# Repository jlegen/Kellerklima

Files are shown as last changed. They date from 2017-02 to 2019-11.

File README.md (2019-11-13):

# Kellerklima
## Arduino-based humidity controller with indoor and outdoor sensors for fan control

I made this device to dry my (and others :) cellars by mostly making use of the times when the *absolute* humidity outdoors is lower than indoors. 
For this, two sensors are used to measure humidity and temperature, indoors and outdoors.
Though this seems to be quite a common design, i only found some rather costly commercial products. This one mostly uses cheap and popular modules.

## Basic principle
Temperature and humidity values from inside and outside are used to calculate the absolute humidity. If the outside is less humid than the inside, the fan is started (or, alternatively, the window is opened, if an opener is used instead of a fan).
There's a maximum fan runtime to be configured. After this time, either the fan is paused, or - using the 2nd relay - a dehumidifier unit can be started for a set period of time.
This repeats until the target humidity value for the inside is reached, or one of the user-defined criterias change:
* fan and dehumidifier only run if the inside humidity is above the trigger value
* fan only runs if inside temperature is above a minimum value
* fan only runs if outside temperature is above a minimum value
* fan and dehumidifier only run if the runtime limit per day (24h) is not reached yet

Defaults are: 
* dew point difference between indoors and outdoors >= 3: switch fan on
* dew point difference between indoors and outdoors < 1: switch fan off
* humidity hysteresis for trigger: 1 
	* indoor humiditity >= <trigger value>: switch fan/dehumidifier on
	* indoor humiditity < <trigger value - 1>: switch fan/dehumidifier off

## Implementation

The regulation makes use of configurable hysteresis values for activation and deactivation, to avoid "flapping", and a fan being turned on and off too quickly.
All parameters can be configured using the rotary encoder and a menu system with the 1602 LCD.
Optionally, if an ESP-01 module with ESP-Link (https://github.com/jeelabs/esp-link) is equipped, all parameters can be set using telnet. 
This ESP-01 module also allows to remotely flash the arduino code of the controller, and to monitor all activities of the control box remotely. Parameters can be defined using simple commands, and also fan or dehumidifier can be switched on and off, overriding the regulation.
the libraries used are commented in the code.

Update: It turned out that the DHT22 sensors are cr*p, they "wear out" quite quickly, showing wrong humidity data after a few weeks.
To be able to make use of better quality I2C sensors like BME280 or SHT31, i added an I2C booster/bus driver IC to allow for the long(er) wires i needed. For me, 10m do work just fine with SHT31, there are reports that up to 100m are possible, too.
Additionally, i did not manage to get the SLIP protocol running reliably using the ESP-Link, but i still regard the ESP-01 as useful, since the arduino not only can be flashed "OTA" using ESP-link, the new version also allows to monitor the arduino's activities using EPS-link's "µC Console", and the whole thing can be controlled remotely using a set of commands to set temperatures and other parameters. 
Next hardware revision should probably use an ESP module as controller... 

Update 2: Meanwhile, the system is running for more than a year in "production". Works like a charm... :-)

# Gallery

box in normal run mode; the LCD is switched off after a few minutes of inactivity

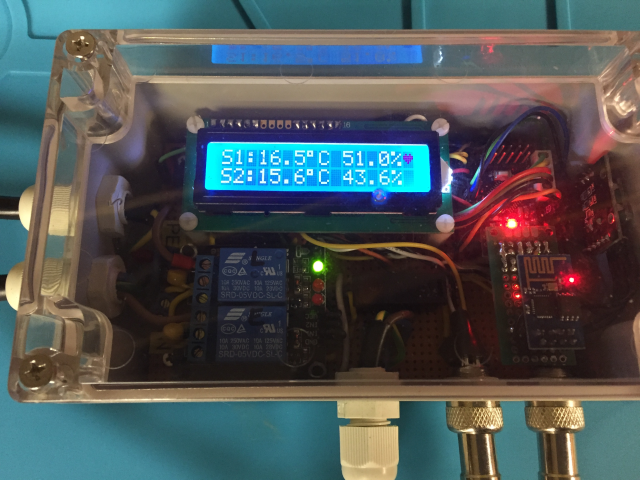
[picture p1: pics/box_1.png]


rotary encoder at the right - is used to scroll through values, testing the relay, and to set most parameters

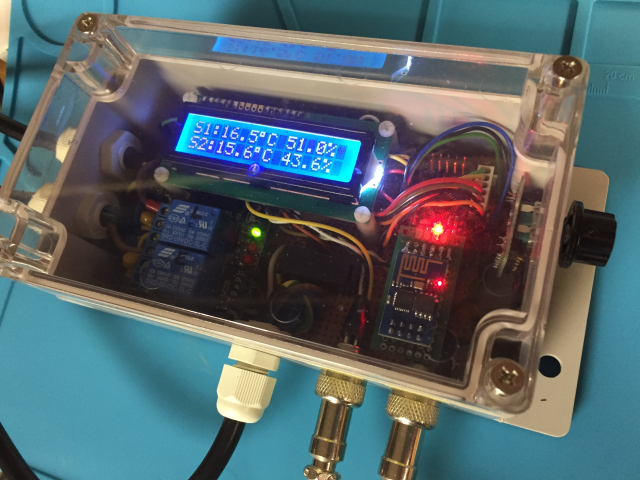
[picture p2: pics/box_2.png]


PCB version finally ready (V1.2)
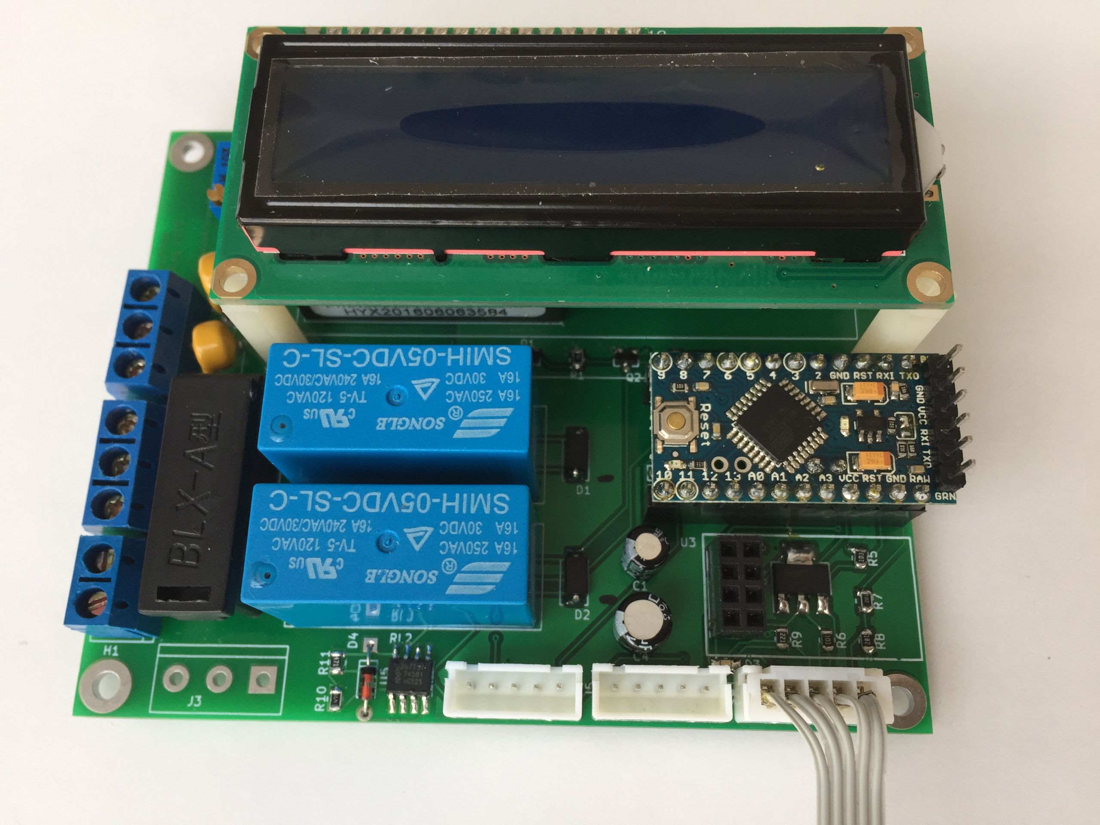
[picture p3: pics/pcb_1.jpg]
1st PCB version


new PCB for sensors - tailored to fit into cheap waterproof boxes (65X58X35mm)
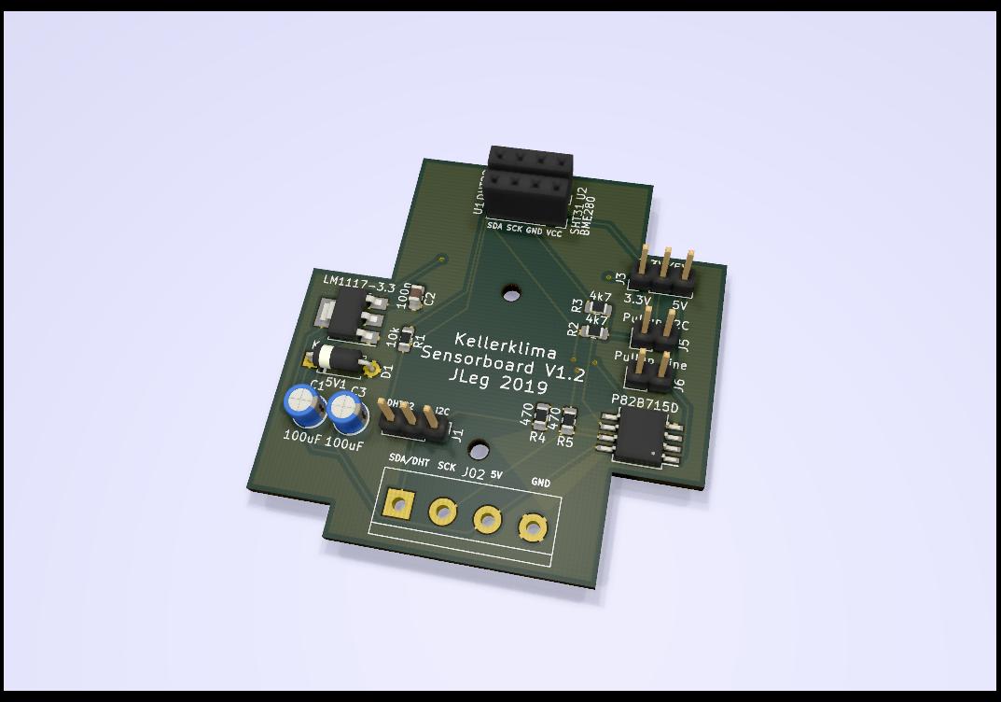
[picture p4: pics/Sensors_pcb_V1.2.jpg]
Sensor pcp 1.2


like these
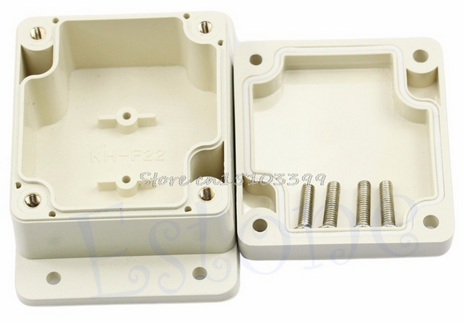
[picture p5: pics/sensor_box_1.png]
box_1

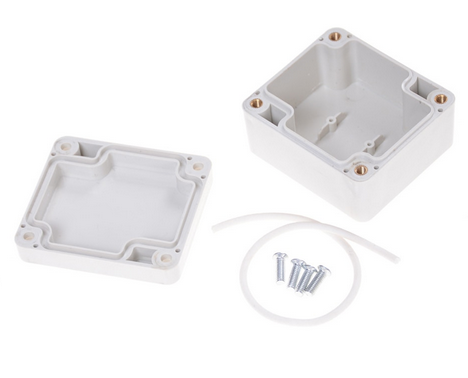
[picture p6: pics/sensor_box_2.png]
box_2


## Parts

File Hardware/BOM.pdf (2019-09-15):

Kellerklima 1.2
Humidity Controller

Main Controller
Arduino Pro Mini | 1 | check position of A4 and A5 (I2C)
Rotary encoder | 1 | generic type or module
Buzzer (passive), 12x9.5RM7.6 | 1
LCD 1602 | 1 | HD44780, parallel/4 bit mode
Case | 1
M12 cable gland (Verschraubung) | 3
SP16/GX16 4p cable connector | 2
PCB | 1 | JLCPCB
Relais 5V, Songle | 2 | SMIH-05V SL-A
Power HLK-PM01 | 1
JST connectors 1x04_P2.50mm | 3
5.1V Zehner | 1
P82B715D I2C Booster | 1
MOV (VDR), 420V | 2
ESP-01 | 1 | optional
Terminal 3p | 3
Terminal 2p | 1
Switch | 1
LM1117-3.3 | 1
BC846BS SOT3 | 2
Fuse holder | 1

Sensors (x 2)
SHT31 module | 2
SP16/GX16 4p cable connector | 2
cable, 4p, shielded (m) | 10
Case | 2
PCB | 2
5.1V Zehner | 2
LM1117-3.3 | 2
P82B715D I2C Booster | 2
Terminal 4p | 2

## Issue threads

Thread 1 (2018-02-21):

netburner and virtualcom

ieee488, 2018-02-21:
I found your post at https://github.com/jeelabs/esp-link/issues/294

Would you explain further how you were able to flash an Arduino and an attached ESP-01 module running esp-link firmware?

jlegen, 2019-02-28:
Uh, sorry, i did not get a notification (and did not deal with this project for some time), so i missed your question. But better late than never...

To flash an arduino (i use this with "pro minis") using ESP-Link, the simplest method is using a "virtual com port driver". Using windows, you might use one of these free drivers:
https://www.hw-group.com/software/hw-vsp3-virtual-serial-port
https://www.netburner.com/virtual-com-port/
They create additional "com ports" (serial ports), e.g. "Com10". They provide a little config window, where you have to enter the IP address and the port of your ESP-Link-module.
For local access/development that's the IP address the router gave the ESP-link (like 192.168.1.55), and the port is "2323".
Then simply chose "com10" in Arduino-IDE for "Upload", and that's it.
I even use this to update units "in the field" (at other locations), using DynamicDNS-IPs - works as well, but should not be left "open" by default...

ieee488, 2019-02-28:
Thank you for the answer!

The link for the Netburner driver is https://www.netburner.com/download/virtual-comm-port-driver-windows-xp-10/

The drivers will be useful.

.

Closed 2019-02-28.

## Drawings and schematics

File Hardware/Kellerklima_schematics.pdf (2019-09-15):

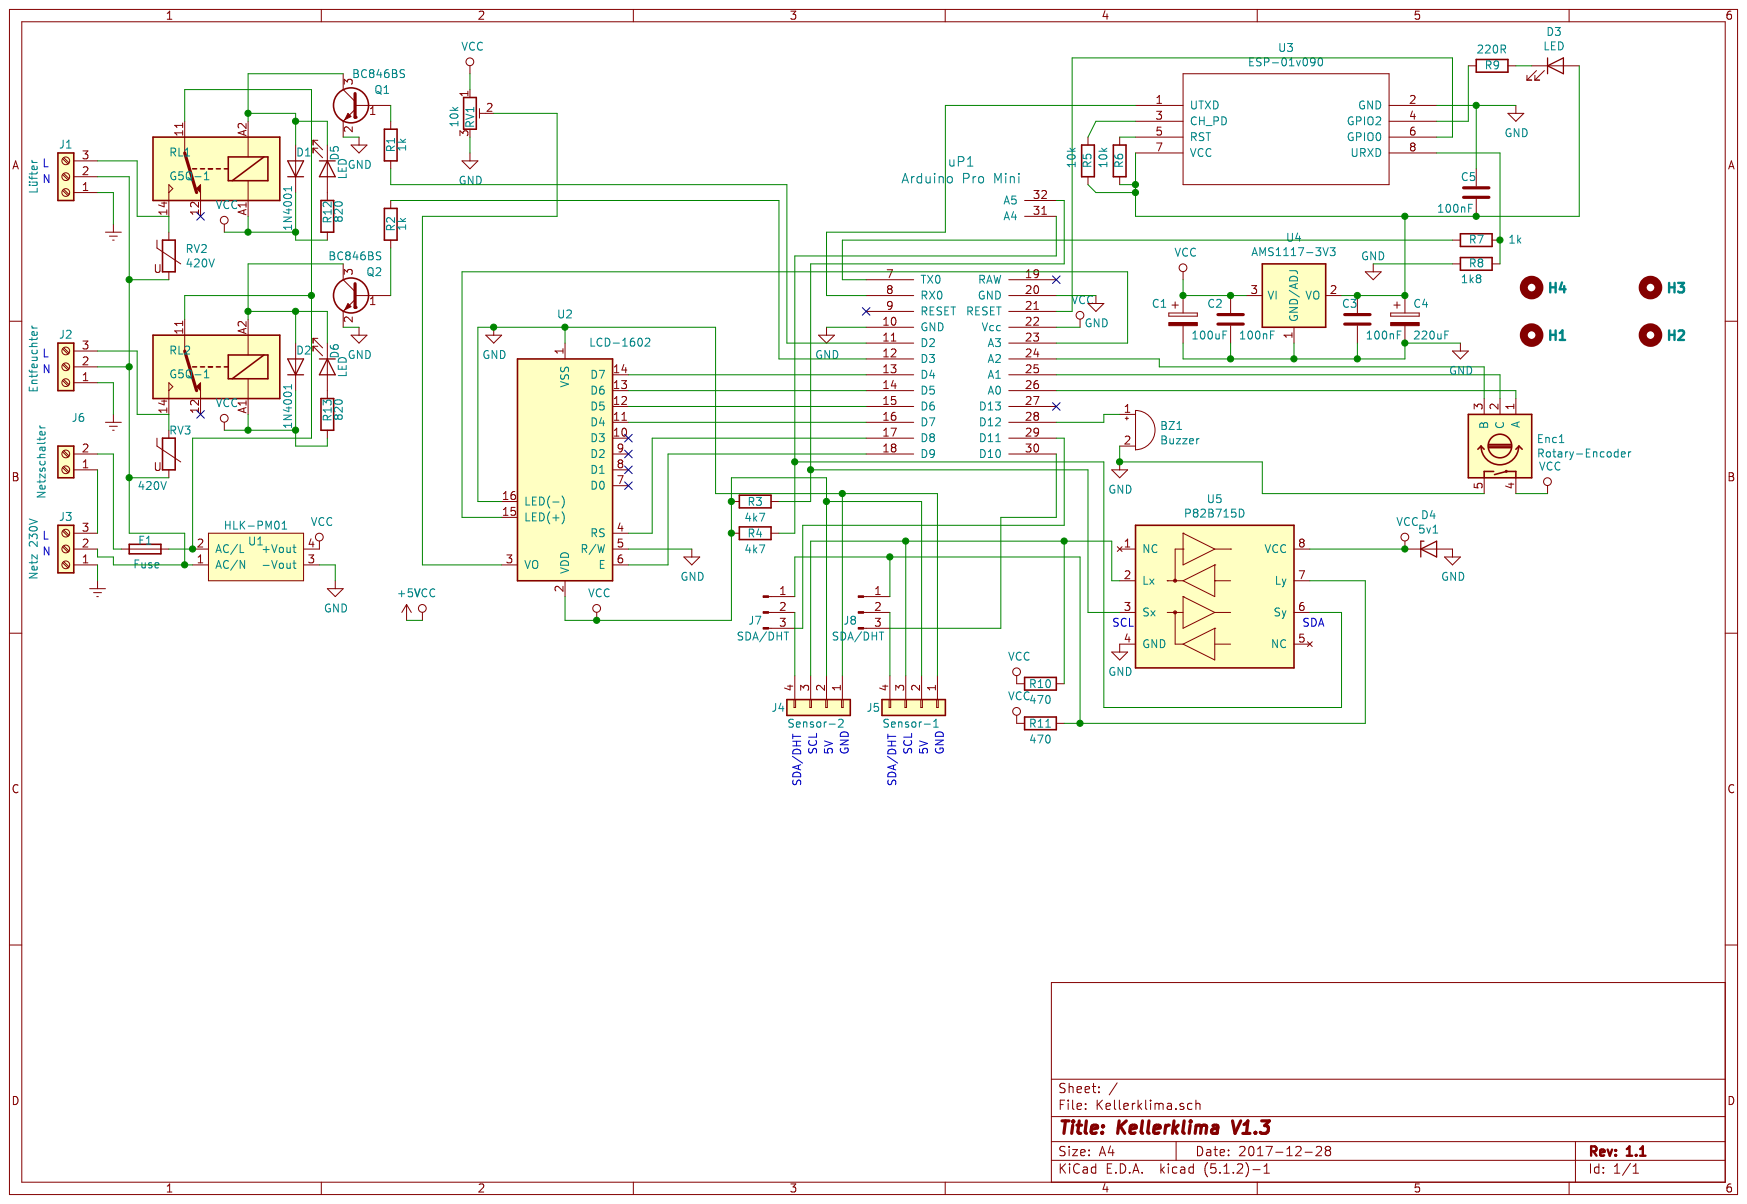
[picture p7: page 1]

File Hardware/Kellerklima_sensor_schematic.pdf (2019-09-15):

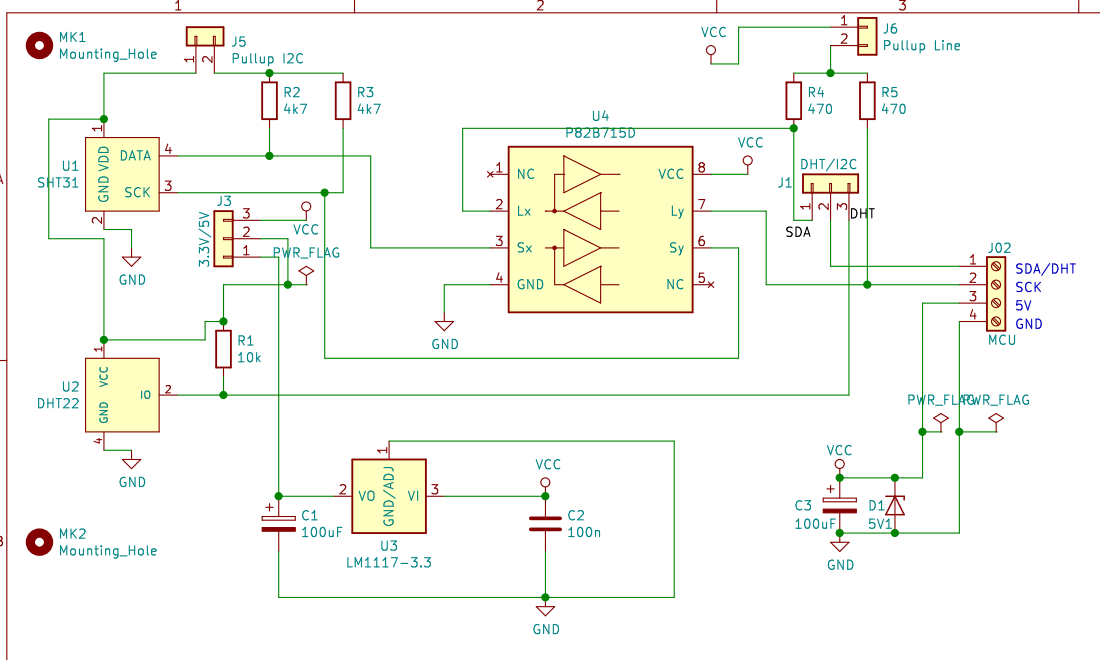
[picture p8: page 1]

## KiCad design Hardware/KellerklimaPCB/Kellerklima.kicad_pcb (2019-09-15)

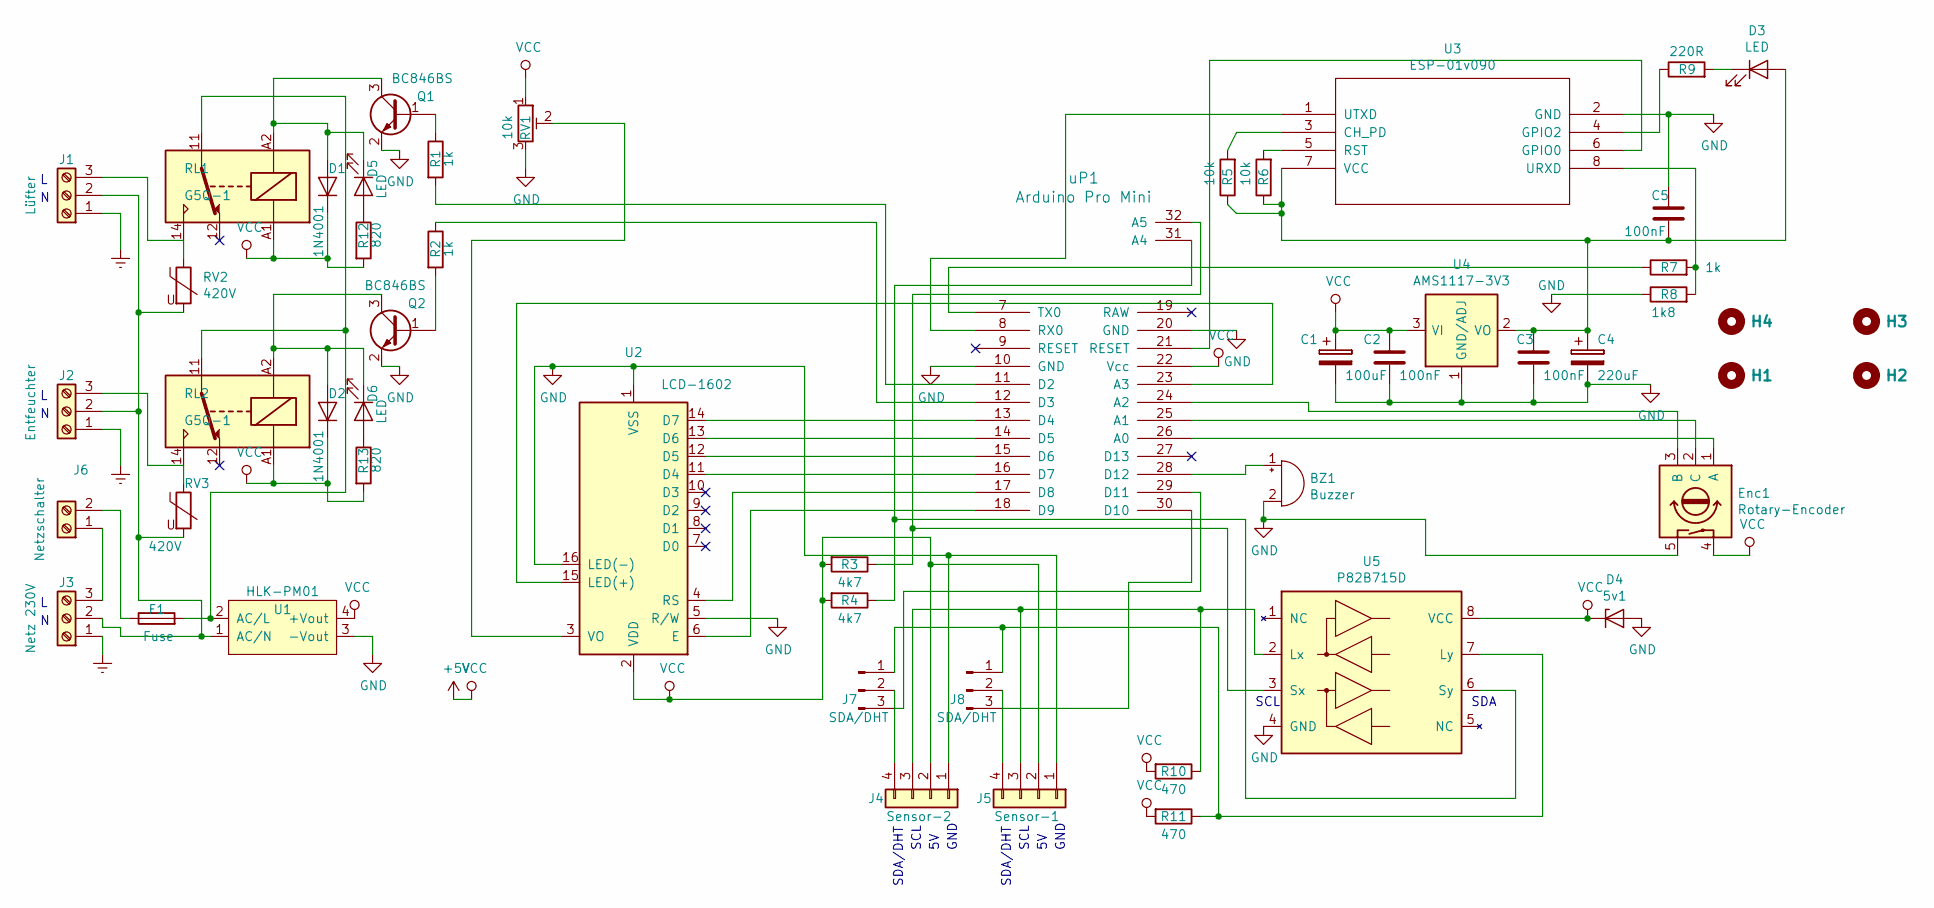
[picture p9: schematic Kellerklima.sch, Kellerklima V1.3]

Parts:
BZ1: Buzzer
C1: 100uF
C2, C3, C5: 100nF
C4: 220uF
D1, D2: 1N4001; D_DO-41_SOD81_P10.16mm_Horizontal
D3, D5, D6: LED
D4: 5v1
Enc1: Rotary-Encoder
F1: Fuse
H1, H2, H3, H4: Hole
J1: Lüfter; TerminalBlock_Phoenix_MKDS1.5-3pol
J2: Entfeuchter; TerminalBlock_Phoenix_MKDS1.5-3pol
J3: Netz 230V; TerminalBlock_Phoenix_MKDS1.5-3pol
J4: Sensor-2
J5: Sensor-1
J6: Netzschalter; TerminalBlock_Phoenix_MKDS1.5-2pol
J7, J8: SDA/DHT
Q1, Q2: BC846BS; SOT-323
R1, R2, R7: 1k
R3, R4: 4k7
R5, R6: 10k
R8: 1k8
R9: 220R
R10, R11: 470
R12, R13: 820
RL1, RL2: G5Q-1; Relay_SPDT_Finder_40.51
RV1: 10k
RV2, RV3: 420V; RV_Disc_D7mm_W3.9mm_P5mm
U1: HLK-PM01; ACDC-Converter_MeanWell-IRM-02-x
U2: LCD-1602; WC1602A
U3: ESP-01v090; PinSocket_2x04_P2.54mm_Vertical
U4: AMS1117-3V3; MPN LM1117
U5: P82B715D
uP1: Arduino Pro Mini

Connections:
+5V: C1.1, C2.1, D1.1 (K), D2.1 (K), D4.1 (K), Enc1.4, J4.2, J5.2, R3.2, R4.2, R10.2, R11.2, R12.2, R13.2, RL1.A1, RL2.A1, RV1.1, U1.4 (+Vout), U2.2 (VDD), U4.3 (VI), U5.8 (VCC), uP1.22 (Vcc)
Earth: J1.1, J2.1, J3.1
GND: BZ1.2 (+), C1.2, C2.2, C3.2, C4.2, C5.1, D4.2 (A), Enc1.5, J4.1, J5.1, Q1.2 (E), Q2.2 (E), R8.1, RV1.3, U1.3 (-Vout), U2.1 (VSS), U2.5 (R/W), U2.16 (LED(-)), U3.2 (GND), U4.1 (GND/ADJ), U5.4 (GND), uP1.10 (GND), uP1.20 (GND)
unnamed: BZ1.1 (-), uP1.28 (D12)
unnamed: C3.1, C4.1, C5.2, D3.2 (A), R5.1, R6.1, U3.7 (VCC), U4.2 (VO)
unnamed: D1.2 (A), D5.1 (K), Q1.3 (C), RL1.A2
unnamed: D2.2 (A), D6.1 (K), Q2.3 (C), RL2.A2
unnamed: D3.1 (K), R9.2
unnamed: D5.2 (A), R12.1
unnamed: D6.2 (A), R13.1
unnamed: Enc1.1 (A), uP1.26 (A0)
unnamed: Enc1.2 (C), uP1.25 (A1)
unnamed: Enc1.3 (B), uP1.24 (A2)
unnamed: F1.1, J6.2
unnamed: F1.2, RL1.11, RL2.11, U1.2 (AC/L)
unnamed: J1.2, J2.2, J3.2, RV2.2, RV3.2, U1.1 (AC/N)
unnamed: J1.3, RL1.14, RV2.1
unnamed: J2.3, RL2.14, RV3.1
unnamed: J3.3, J6.1
unnamed: J4.3, J5.3, R10.1, U5.2 (Lx)
unnamed: J4.4, J7.2
unnamed: J5.4, J8.2
unnamed: J7.1, J8.1, R11.1, U5.7 (Ly)
unnamed: J7.3, uP1.29 (D11)
unnamed: J8.3, uP1.30 (D10)
unnamed: Q1.1 (B), R1.1
unnamed: Q2.1 (B), R2.2
unnamed: R1.2, uP1.11 (D2)
unnamed: R2.1, uP1.12 (D3)
unnamed: R3.1, U5.3 (Sx), uP1.32 (A5)
unnamed: R4.1, U5.6 (Sy), uP1.31 (A4)
unnamed: R5.2, U3.3 (CH_PD)
unnamed: R6.2, U3.5 (RST)
unnamed: R7.1, uP1.7 (TX0)
unnamed: R7.2, R8.2, U3.8 (URXD)
unnamed: R9.1, U3.4 (GPIO2)
unnamed: RV1.2, U2.3 (VO)
unnamed: U2.4 (RS), uP1.17 (D8)
unnamed: U2.6 (E), uP1.18 (D9)
unnamed: U2.11 (D4), uP1.16 (D7)
unnamed: U2.12 (D5), uP1.15 (D6)
unnamed: U2.13 (D6), uP1.14 (D5)
unnamed: U2.14 (D7), uP1.13 (D4)
unnamed: U2.15 (LED(+)), uP1.23 (A3)
unnamed: U3.1 (UTXD), uP1.8 (RX0)
unnamed: U3.6 (GPIO0), uP1.21 (RESET)

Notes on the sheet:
SDA
SCL
SDA/DHT
GND

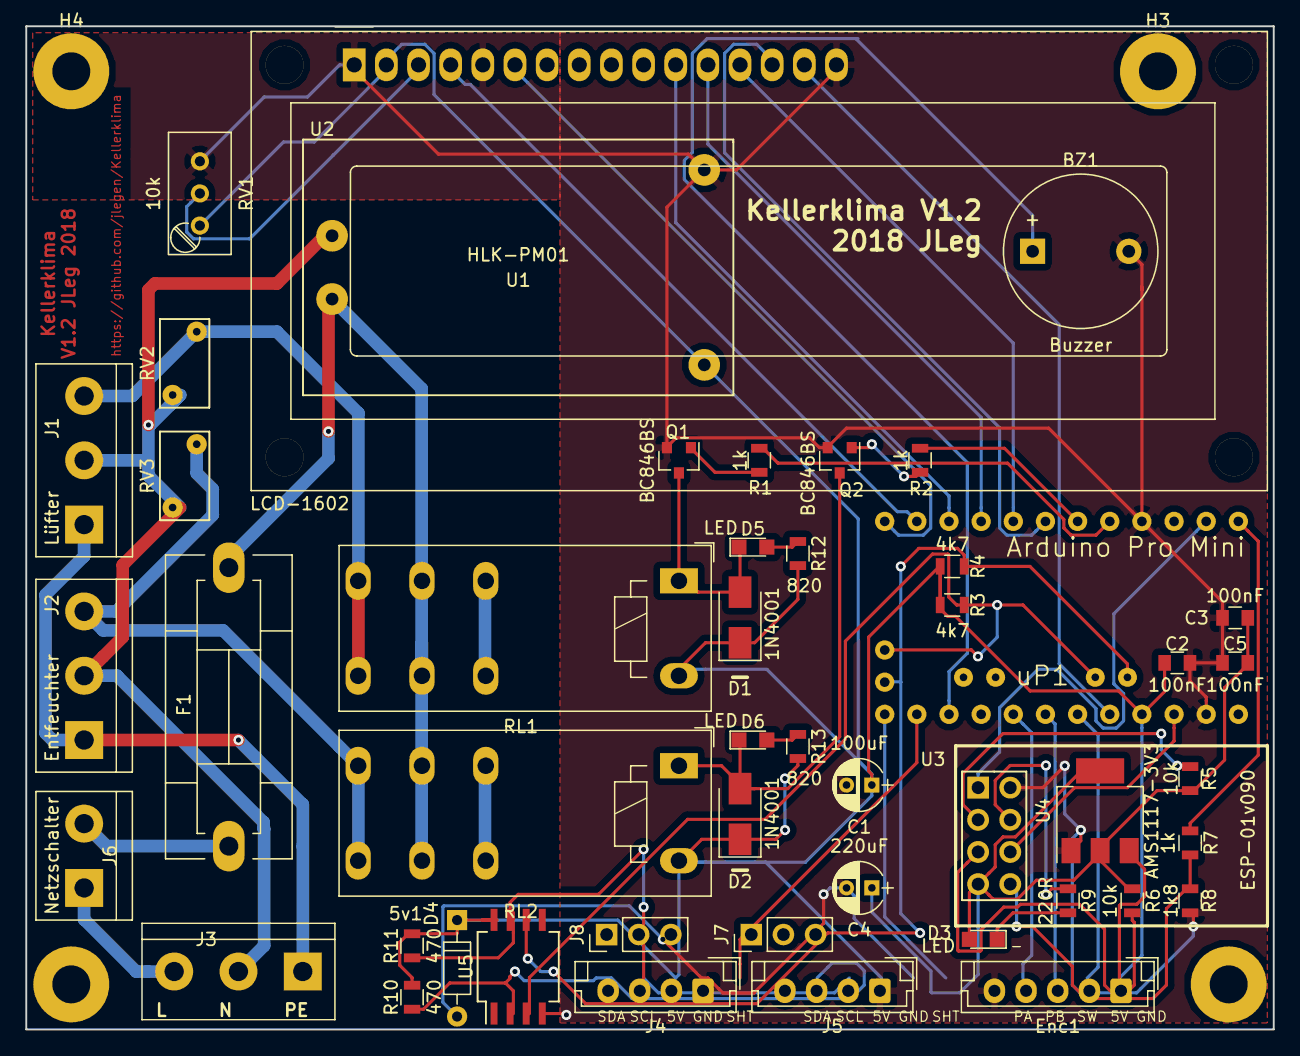
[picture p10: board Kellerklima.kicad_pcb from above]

Board: 2 copper layers, 98.6 x 79.2 mm, 52 parts (0 on the bottom side), 46 nets.

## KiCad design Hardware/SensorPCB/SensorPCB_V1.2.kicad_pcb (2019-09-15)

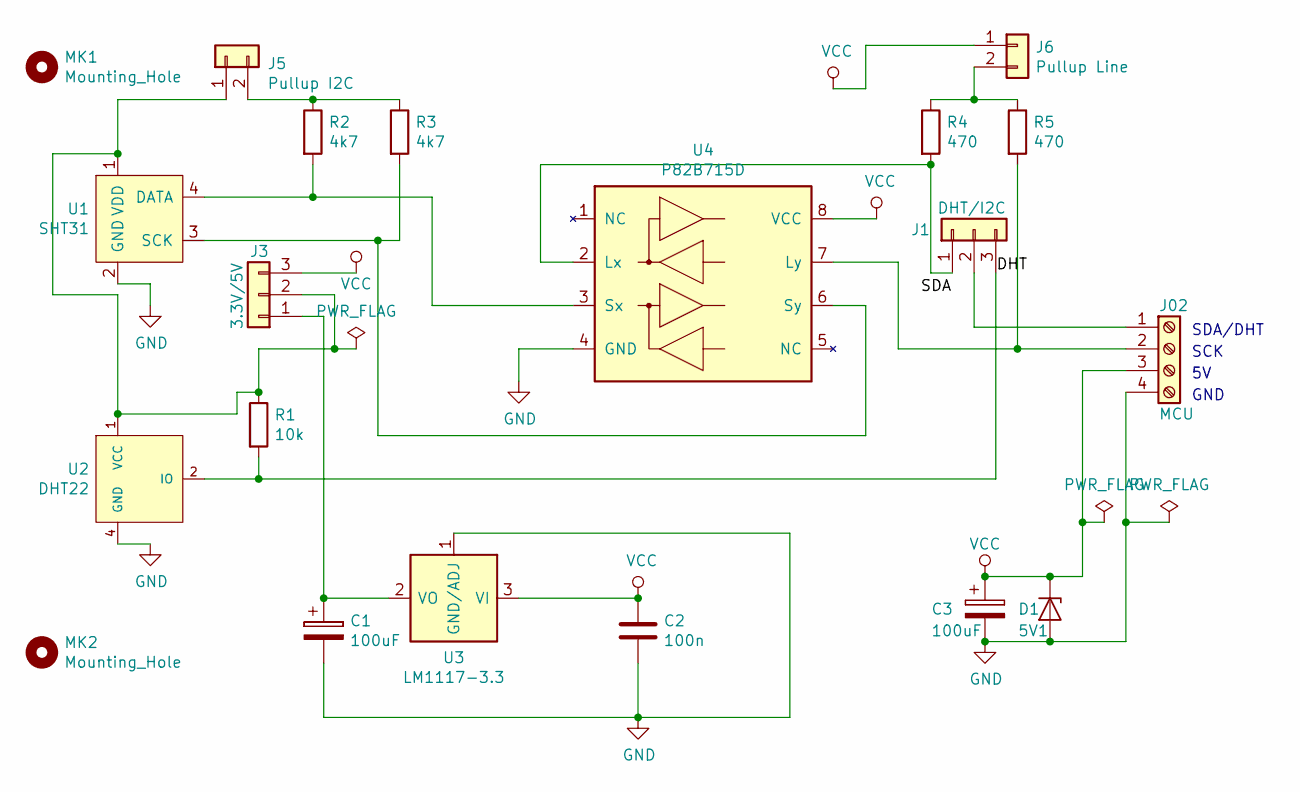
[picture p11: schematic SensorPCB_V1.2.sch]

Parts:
C1, C3: 100uF; CP_Radial_D4.0mm_P2.00mm
C2: 100n; C_0805_2012Metric_Pad1.15x1.40mm_HandSolder
D1: 5V1; D_A-405_P7.62mm_Horizontal
J1: DHT/I2C; PinHeader_1x03_P2.54mm_Vertical
J02: MCU; TerminalBlock_bornier-4_P5.08mm
J3: 3.3V/5V; PinHeader_1x03_P2.54mm_Vertical
J5: Pullup I2C; PinHeader_1x02_P2.54mm_Vertical
J6: Pullup Line; PinHeader_1x02_P2.54mm_Vertical
MK1, MK2: Mounting_Hole; MountingHole_2.2mm_M2
R1: 10k; R_0805_2012Metric_Pad1.15x1.40mm_HandSolder
R2, R3: 4k7; R_0805_2012Metric_Pad1.15x1.40mm_HandSolder
R4, R5: 470; R_0805_2012Metric_Pad1.15x1.40mm_HandSolder
U1: SHT31; PinSocket_1x04_P2.54mm_Vertical
U2: DHT22; PinSocket_1x04_P2.54mm_Vertical
U3: LM1117-3.3; SOT-223-3_TabPin2
U4: P82B715D; SO-8_5.3x6.2mm_P1.27mm

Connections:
/DHT: J1.3, R1.2, U2.2 (IO)
GND: C1.2, C2.2, C3.2, D1.2 (A), J02.4, U1.2 (GND), U2.4 (GND), U3.1 (GND/ADJ), U4.4 (GND)
unnamed: C1.1, J3.1, U3.2 (VO)
unnamed: J1.1, R4.2, U4.2 (Lx)
unnamed: J1.2, J02.1
unnamed: J02.2, R5.2, U4.7 (Ly)
unnamed: J3.2, J5.1, R1.1, U1.1 (VDD), U2.1 (VCC)
unnamed: J5.2, R2.1, R3.1
unnamed: J6.2, R4.1, R5.1
unnamed: R2.2, U1.4 (DATA), U4.3 (Sx)
unnamed: R3.2, U1.3 (SCK), U4.6 (Sy)
VCC: C2.1, C3.1, D1.1 (K), J02.3, J3.3, J6.1, U3.3 (VI), U4.8 (VCC)

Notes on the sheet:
SDA/DHT
SCK
GND

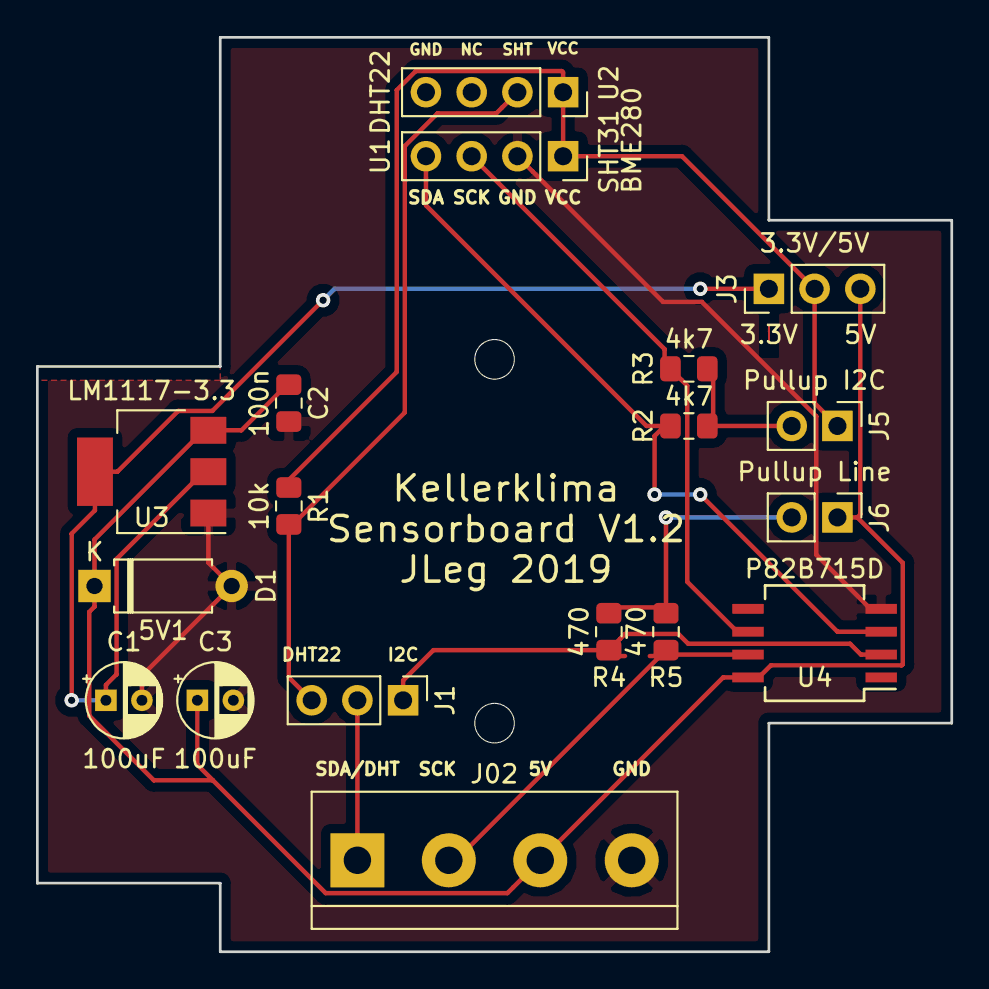
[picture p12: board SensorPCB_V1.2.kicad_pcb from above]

Board: 2 copper layers, 50.8 x 50.8 mm, 20 parts (0 on the bottom side), 12 nets.

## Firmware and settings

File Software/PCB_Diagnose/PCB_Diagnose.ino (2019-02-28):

//#define DHTPIN_I 10     // Pin Innensensor S1
//#define DHTPIN_O 11     // Pin Aussensensor S2
//#define SENSI2C1 0x76 // use I2C sensors => BME280 breakouts
//#define SENSI2C2 0x77
#define SHTI2C1 0x44 // use I2C sensors => SHT31 breakouts
#define SHTI2C2 0x45

//#define TWI_FREQ 10000L;
#include <Wire.h>
#include <ClickEncoder.h>                   // https://github.com/0xPIT/encoder
#include <TimerOne.h>                       // https://github.com/PaulStoffregen/TimerOne

#ifdef DHTPIN_I
 //#include "cactus_io_DHT22.h";
 #include "DHT.h"                           
#endif
#ifdef SENSI2C1
 #include "cactus_io_BME280_I2C.h";
 #define I2C_SENSOR 1         
#endif
#ifdef SHTI2C1
 #include "cactus_io_SHT31.h";         
 #define I2C_SENSOR 1         
#endif

#define Relais_L 2     // Pin Lüfter/Klappe
#define Relais_E 3     // Pin Entfeuchter
#define ActLED 13      // Pin LED (Messung)

uint8_t my_relays[] = {Relais_L, Relais_E};

//#define RelaysLowActive // trigger relays with low signal


// LCD
//#define LCD_I2C  // use I2C LCD - parallel otherwise
// I2C LCD config
#define LCD_ADDR 0x27
#define LCD_CHARS 16
#define LCD_LINES  2
// parallel LCD config
#define LCD_RS     8 
#define LCD_EN     9
#define LCD_D4     7   
#define LCD_D5     6   
#define LCD_D6     5   
#define LCD_D7     4   
#define LCD_LED    17
// LCD R/W pin to ground
// LCD VSS pin to ground
// LCD VCC pin to 5V
// 10K resistor ends to +5V and ground

#ifdef LCD_I2C
 #define LCD_ON lcd.backlight(); 
 #define LCD_OFF lcd.noBacklight(); 
#else
 #define LCD_ON lcd.display(); digitalWrite(LCD_LED, true); 
 #define LCD_OFF lcd.noDisplay(); digitalWrite(LCD_LED, false); 
#endif

// I2C LCD
// Set the LCD address to 0x27 for a 16 chars and 2 line display
#ifdef LCD_I2C
 #include <LiquidCrystal_I2C.h>
 LiquidCrystal_I2C lcd(LCD_ADDR, LCD_CHARS, LCD_LINES);
#else
 #include <LiquidCrystal.h>
 LiquidCrystal lcd(LCD_RS, LCD_EN, LCD_D4, LCD_D5, LCD_D6, LCD_D7);
#endif


// Sensortyp
//#define DHTTYPE DHT11   // DHT 11
//#define DHTTYPE DHT21   // DHT 21 (AM2301)
#define DHTTYPE_I DHT22   // DHT 22  (AM2302), AM2321
#define DHTTYPE_O DHT22   // DHT 22  (AM2302), AM2321


#ifdef DHTPIN_I
 DHT sens_i(DHTPIN_I, DHTTYPE_I);
 DHT sens_o(DHTPIN_O, DHTTYPE_O);
 //DHT22 sens_i(DHTPIN_I);
 //DHT22 sens_o(DHTPIN_O);
#endif
#ifdef SENSI2C1
 BME280_I2C sens_i(SENSI2C1); 
 BME280_I2C sens_o(SENSI2C2); 
#endif
#ifdef SHTI2C1
 cactus_io_SHT31 sens_i(SHTI2C1); 
 cactus_io_SHT31 sens_o(SHTI2C2); 
#endif


// ClickEncoder 
// https://github.com/0xPIT/
//
#define r_button 16                //rotary encoder pushbutton, PB1
#define r_pha 15                   //rotary encoder phase A, PB2
#define r_phb 14                   //rotary encoder phase B, PB3

int16_t encMovement;
int16_t encAbsolute;
int16_t encLastAbsolute = -1;
//bool lastEncoderAccelerationState = false;
unsigned long prev_millis = 0;
unsigned long curr_millis = 0;
unsigned long milliMil = 0;

float hum_i = 0;
float hum_o = 0;
float temp_i = 0;
float temp_o = 0;

ClickEncoder Encoder(r_pha, r_phb, r_button, 2); // 2,3,4 = clicks per step (notches)

// Pieper
#define BUZZER 12        // pin for buzzer
//#define TONE_ON digitalWrite(BUZZER, true) 
//#define TONE_OFF digitalWrite(BUZZER, false) 
//passive buzzer - only when on PWM pin! (1, 9, 10, 12, 13)
#define TONE_ON tone(BUZZER, 1200)
#define TONE_OFF noTone(BUZZER)

// custom chars
enum Icons {
  IconLeft = 0,
  IconRight = 1,
  IconBack = 2,
  IconBlock = 3,
  IconHeart = 4,
};

byte heart[8] = {0x0, 0xa, 0x1f, 0x1f, 0xe, 0x4, 0x0};

byte left[8] = {
  0b00010,
  0b00110,
  0b01110,
  0b11110,
  0b01110,
  0b00110,
  0b00010,
  0b00000
};

byte right[8] = {
  0b01000,
  0b01100,
  0b01110,
  0b01111,
  0b01110,
  0b01100,
  0b01000,
  0b00000
};

byte back[8] = {
  0b00000,
  0b00100,
  0b01100,
  0b11111,
  0b01101,
  0b00101,
  0b00001,
  0b00000
};

byte block[8] = {
  0b00000,
  0b11110,
  0b11110,
  0b11110,
  0b11110,
  0b11110,
  0b11110,
  0b00000
};

void timerIsr()
{
  Encoder.service();
}

// Relais schalten
void set_relay(uint8_t relay, bool trig) {
#ifdef RelaysLowActive
  digitalWrite(my_relays[relay], !trig);  // set = true => relais = LOW
#else
  digitalWrite(my_relays[relay], trig);  // set = true => relais = LOW
#endif
}

void buzzer(uint16_t dura) {
#ifdef BUZZER
  if (dura == 0) { // 0 = Alert
    while ((millis() - curr_millis) <= 3000) {
     TONE_ON;
     delay(400);
     TONE_OFF;
     delay(400);
    }
  } else {
    TONE_ON;
    delay(dura);
    TONE_OFF;
    delay(dura);
    TONE_ON;
    delay(dura);
    TONE_OFF;
  }
#endif
}

void lcdPrintDouble(double val, uint8_t precision = 1, uint8_t lpad=0) {
char tmp[6];
  dtostrf(val,lpad,precision,tmp);
  lcd.print(tmp);
}

void setup() {
  pinMode(ActLED, OUTPUT);
  pinMode(Relais_L, OUTPUT);
  pinMode(Relais_E, OUTPUT);
#ifdef BUZZER  
 pinMode(BUZZER, OUTPUT);
#endif

  //Wire.begin(); // I2C-Scanner

  //Wire.setClock(400000L) 
  //Wire.setClock(100000L) // default
  //Wire.setClock(10000L) 

  //    long CPU_FREQ = 12000000L;
  //    TWBR = ((CPU_FREQ / 100000L) - 16) / 2; // 100KB/s default

  // Alles aus
  set_relay(0, false);              // Lüfter ausschalten
  set_relay(1, false);              // Entf. ausschalten

  Timer1.initialize(1000);
  Timer1.attachInterrupt(timerIsr);

  // LCD
#ifdef LCD_I2C
  lcd.begin();
#else
  pinMode(LCD_LED, OUTPUT);
  lcd.begin(LCD_CHARS, LCD_LINES);
#endif

  lcd.createChar(IconHeart, heart);
  lcd.createChar(IconLeft,  left);
  lcd.createChar(IconRight, right);
  lcd.createChar(IconBack,  back);
  lcd.createChar(IconBlock, block);


  lcd.clear();
  //lcd.backlight();
  LCD_ON;
  delay(1000);
  LCD_OFF;
  delay(2000);
  LCD_ON;
  //         0123456789012345
  lcd.setCursor(0, 0);
  lcd.print("LCD ");
  lcd.setCursor(4, 0);
  lcd.write(IconHeart);
  lcd.write(IconLeft);
  lcd.write(IconRight);
  lcd.write(IconBack);
  lcd.write(IconBlock);

  lcd.setCursor(0, 1);
  lcd.print("Umlaute \365 \341 \357 \337");
  buzzer(150);
  delay(3000);

 Serial.begin(57600);

  // initialize Sensors
#ifdef DHTPIN_I
  sens_i.begin();
  sens_o.begin();
#endif
#ifdef I2C_SENSOR
 if (!sens_i.begin()) {
  Serial.println("Error I2C for sens_i!");
 }
 if (!sens_o.begin()) {
  Serial.println("Error I2C for sens_o!");
 }
#endif

 //lcd.clear();
}

void loop() {
  byte i2c_error, i2c_address;
  int i2c_nDevices;
 
  curr_millis = millis();
  milliMil = (unsigned long) curr_millis - prev_millis;

  if (milliMil >= (unsigned long)3000 ) {
    prev_millis = curr_millis;
    digitalWrite(ActLED, true);
#ifdef DHTPIN_I
    // DHT22
    // Reading temperature or humidity takes about 250 milliseconds!
    // Sensor readings may also be up to 2 seconds 'old' (its a very slow sensor)
    hum_i = sens_i.readHumidity();
    hum_o = sens_o.readHumidity();
    // Read temperature as Celsius (the default)
    temp_i = sens_i.readTemperature();
    temp_o = sens_o.readTemperature();
    
    /*
    sens_i.readHumidity();
    sens_o.readHumidity();
    sens_i.readTemperature();
    sens_o.readTemperature();
    hum_i = sens_i.humidity;
    hum_o = sens_o.humidity;
    temp_i = sens_i.temperature_C;
    temp_o = sens_o.temperature_C;
    */
#endif
#ifdef I2C_SENSOR
    // BME280, SHT31
    // setTempCal(float) Allows you to define a temp calibration offset if it reads high
    hum_i = sens_i.getHumidity();
    hum_o = sens_o.getHumidity();
    temp_i = sens_i.getTemperature_C();
    temp_o = sens_o.getTemperature_C();
#endif

    Serial.print("Sensor 1 Temp: ");
    Serial.println(temp_i);
    Serial.print("Sensor 1 Hum: ");
    Serial.println(hum_i);
    Serial.print("Sensor 2 Temp: ");
    Serial.println(temp_o);
    Serial.print("Sensor 2 Hum: ");
    Serial.println(hum_o);

    /*lcd.clear();
    lcd.setCursor(0, 0);
    lcd.print(temp_i);
    lcd.print(" ");
    lcd.print(hum_i);
    lcd.setCursor(0, 1);
    lcd.print(temp_o);
    lcd.print(" ");
    lcd.print(hum_o);
*/
  }

  encMovement = Encoder.getValue();
  if (encMovement) {
    prev_millis = curr_millis;  // INTERVAL time for showing data
    encAbsolute += encMovement;
    lcd.setCursor(0, 1);
    lcd.print("Encoder: ");
    //lcd.setCursor(10,1);
    lcd.print(encAbsolute);
    lcd.print(" ");
  }
  
  // handle button
  switch (Encoder.getButton()) {
    case ClickEncoder::Clicked:
    lcd.clear();
    lcd.setCursor(0, 0);
    lcd.print("Beeping Buzzer!");
    buzzer(40);
    break;

    case ClickEncoder::Held:
    lcd.clear();
    set_relay(0, true);
    lcd.setCursor(0, 0);
    lcd.print("Relay 1 On!");
    delay(1000);
    set_relay(0, false);
    lcd.setCursor(0, 0);
    lcd.print("Relay 1 Off!");
    delay(1000);
    set_relay(1, true);
    lcd.setCursor(0, 1);
    lcd.print("Relay 2 On!");
    delay(1000);
    set_relay(1, false);
    lcd.setCursor(0, 1);
    lcd.print("Relay 2 Off!");
    delay(1000);
    break;

    case ClickEncoder::DoubleClicked:
    lcd.clear();
    lcd.home();
    lcd.setCursor(0, 0);
    lcd.print("S1: ");
    lcd.print(hum_i,1);
    lcd.print(" ");
    lcdPrintDouble(temp_i, 1, 4);
    lcd.setCursor(0, 1);
    lcd.print("S2: ");
    lcd.print(hum_o,1);
    lcd.print(" ");
    lcdPrintDouble(temp_o, 1, 4);
    delay(2000);
    break;

  }

i2c_nDevices =0 ;

if (milliMil >= (unsigned long)5000 ) {
  lcd.clear();
  for(i2c_address = 1; i2c_address < 127; i2c_address++ ) 
  {
    Wire.beginTransmission(i2c_address);
    i2c_error = Wire.endTransmission();

    if (i2c_error == 0)
    {
      //Serial.print("I2C device found at address 0x");
      lcd.print("I2C device: ");
      if (i2c_address<16) 
        lcd.print("0");
      lcd.print(i2c_address,HEX);
      lcd.print(" ");

      i2c_nDevices++;
    }
    else if (i2c_error==4) {
      lcd.print("error at 0x");
      if (i2c_address<16) 
        lcd.print("0");
      lcd.print(i2c_address,HEX);
    }    
  }
  if (i2c_nDevices == 0) {
    lcd.print("No I2C-dev found");
  } else {
    lcd.print("I2C devices: ");
    lcd.print(i2c_nDevices);
  }
}
delay(300);
digitalWrite(ActLED, false);



}

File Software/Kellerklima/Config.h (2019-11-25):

//
// most configurable stuff here...
//
#define VERSION  1.3

//#define DHTPIN_I 10     // Pin Innensensor S1
//#define DHTPIN_O 11     // Pin Aussensensor S2
//#define BMEI2C1 0x76 // use I2C sensors => BME280 breakouts
//#define BMEI2C2 0x77
#define SHTI2C1 0x44  // use I2C sensors => SHT31 breakouts
#define SHTI2C2 0x45
#define Relais_L 2     // Pin Lüfter/Klappe
#define Relais_E 3     // Pin Entfeuchter
#define ActLED 13      // Pin LED (Messung)

#define AINTV 500      // Intervall für Aktivitätsanzeige

//#define RelaysLowActive 1 // trigger relays with low signal (PCB1.2: do not define)

// use esp-link?
//#define HAVE_ESPLINK true
#ifdef HAVE_ESPLINK
 // Change to your own Thingspeak API key
 char *api_key = "X436YTGNCGV1SFG8";
 char *api_host = "184.106.153.149";
 #define BUFLEN 266
 #define SEND_MAX_RETRY 4	// retry of REST requests 
 //bool sync_done = false;    // status of communication with ESP-link 
 bool wifiConnected = false;  // status of communication with ESP-link
#endif

// LCD
#define LCD_CHARS 16
#define LCD_LINES  2
//#define LCD_I2C  // use I2C LCD - parallel otherwise
// I2C LCD config
#define LCD_ADDR 0x27
// parallel LCD config
#define LCD_RS     8 
#define LCD_EN     9
#define LCD_D4     7   
#define LCD_D5     6   
#define LCD_D6     5   
#define LCD_D7     4   
#define LCD_LED    17    // pin to switch backlight
// LCD R/W pin to ground
// LCD VSS pin to ground
// LCD VCC pin to 5V
// 10K resistor ends to +5V and ground

#define BACKLIGHT_OFF 180000 // switch off backlight (3min)
#ifdef LCD_I2C
 #define LCD_ON lcd.backlight(); lcd_on = true;
 #define LCD_OFF lcd.noBacklight(); lcd_on = false;
#else
 #define LCD_ON lcd.display(); digitalWrite(LCD_LED, true); lcd_on = true;
 #define LCD_OFF lcd.noDisplay(); digitalWrite(LCD_LED, false); lcd_on = false;
#endif

// ClickEncoder 
// https://github.com/0xPIT/
//
#define r_button 16                //rotary encoder pushbutton, PB1
#define r_pha 15                   //rotary encoder phase A, PB2
#define r_phb 14                   //rotary encoder phase B, PB3

int16_t encMovement;
int16_t encAbsolute;
int16_t encLastAbsolute = -1;
//bool lastEncoderAccelerationState = false;

ClickEncoder Encoder(r_pha, r_phb, r_button, 2); // 2,3,4 = clicks per step (notches)

// Pieper
#define BUZZER 12 // pin for buzzer
//#define TONE_ON digitalWrite(BUZZER, true) 
//#define TONE_OFF digitalWrite(BUZZER, false) 
//passive buzzer - only when on PWM pin! (1, 9, 10, 12, 13) (PCB 1.2)
#define TONE_ON tone(BUZZER, 1200)
#define TONE_OFF noTone(BUZZER)

#define SERIAL_BAUD 57600
#define EEPROM_ADDR 10  // start address for avr eeprom 

// equivalent to F() macro, also works with lcd.print()
#define FS(x) (__FlashStringHelper*)(x)   // return string from flash
#define FPL(x); lcd.print(FS(x));         // print flash string on LCD
#define FT(x,y);  const char x[] PROGMEM = {y};  // shorter flash string defs

// Sensortyp
//#define DHTTYPE_I DHT11   // DHT 11
//#define DHTTYPE_O DHT11   // DHT 21 (AM2301)
#define DHTTYPE_I DHT22   // DHT 22  (AM2302), AM2321
#define DHTTYPE_O DHT22   // DHT 22  (AM2302), AM2321

// define language
#define GERMAN
//#define ENGLISH

#define FAN 0    // device index
#define DEHYD 1

#define TEMP_HYSTERESIS 1  // universal hysteresis to be used for temperature measures (min. inner/outer temp)

#define ARRAY_SIZE(x) sizeof(x)/sizeof(x[0])

#ifdef GERMAN
const PROGMEM char cmd_0[] = {"r1"};
const PROGMEM char cmd_1[] = {"r2"};
const PROGMEM char cmd_2[] = {"hum"};
const PROGMEM char cmd_3[] = {"tempi"};
const PROGMEM char cmd_4[] = {"tempo"};
const PROGMEM char cmd_5[] = {"max"};
const PROGMEM char cmd_6[] = {"int"};
const PROGMEM char cmd_7[] = {"hysthum"};
const PROGMEM char cmd_8[] = {"dtauon"};
const PROGMEM char cmd_9[] = {"dtauoff"};
const PROGMEM char cmd_10[] = {"offseti"};
const PROGMEM char cmd_11[] = {"offseto"};
const PROGMEM char cmd_12[] = {"save"};
const PROGMEM char cmd_13[] = {"hilfe"};

const PROGMEM char hlp_0[] = {"Luefter r1=1: an | r1=0: aus"};
const PROGMEM char hlp_1[] = {"Entfeuchter r2=1: an | r2=0: aus"};
const PROGMEM char hlp_2[] = {"Feuchte-Schwellwert (%)"};
const PROGMEM char hlp_3[] = {"Mindest-Temperatur 'Innen'"};
const PROGMEM char hlp_4[] = {"Mindest-Temperatur 'Aussen'"};
const PROGMEM char hlp_5[] = {"maximale Geraetelaufzeit pro 24h (Min.)"};
const PROGMEM char hlp_6[] = {"Messintervall (Sek.)"};
const PROGMEM char hlp_7[] = {"Hysterese Feuchteschwellwert (%)"};
const PROGMEM char hlp_8[] = {"Taupunktdifferenz ein (K)"};
const PROGMEM char hlp_9[] = {"Taupunktdifferenz aus (K)"};
const PROGMEM char hlp_10[] = {"Temperaturoffset 'Innen' (K)"};
const PROGMEM char hlp_11[] = {"Temperaturoffset 'Aussen' (K)"};
const PROGMEM char hlp_12[] = {"Speichern aller Parameter"};
const PROGMEM char hlp_13[] = {""};
#endif
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

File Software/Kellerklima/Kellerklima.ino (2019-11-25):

// Lüftungssteuerung V1.3
// (c)2016-19 jleg99@gmail.com
//
// adapt settings in Config.h
//
// switches a fan and/or damper, when a configurable level of humidity is measured by S1, and
// S2 reads a lower absolute humidity.
// If a dehydrator is connected and configured, it is enabled after a configurable fan runtime
// passed without reaching the set humidity level.
// 
// tested with:
//   - DHT22 sensors
//   - SHT31 sensors
//   - I2C-LCD 16x2
//   - parallel LCD 16x2
//   - ESP-01 with esp-link 3.0.14 (using 32Mbit flash)
// prepared for (untested):
//   - LCDs of other sizes
//   - BME280 sensors
//
// remote flash if ESP is attached: use "Netburner Virtual Comport" (create new com port for every flash)
// 

#include <avr/pgmspace.h>
#include <Wire.h>
#include <ClickEncoder.h>                   // https://github.com/0xPIT/encoder
#include <TimerOne.h>                       // https://github.com/PaulStoffregen/TimerOne
#include <Menu.h>                           // https://github.com/0xPIT/menu
#include <EEPROM.h>

#include "Config.h"

#if defined DHTPIN_I || defined DHTPIN_O
 #include "DHT.h"
#endif
#if defined BMEI2C1 || defined BMEI2C2
 #include "cactus_io_BME280_I2C.h";         // http://cactus.io/hookups/sensors/barometric/bme280/hookup-arduino-to-bme280-barometric-pressure-sensor
#endif
#if defined SHTI2C1 || defined SHTI2C2
 #include "cactus_io_SHT31.h";              // http://cactus.io/hookups/sensors/temperature-humidity/sht31/hookup-arduino-to-sensirion-SHT31-temp-humidity-sensor
#endif

#if defined BMEI2C1 || defined SHTI2C1
 #define I2C_SENSOR1 1
#endif
#if defined BMEI2C2 || defined SHTI2C2
 #define I2C_SENSOR2 1
#endif


// I2C LCD
// Set the LCD address to 0x27 for a 16 chars and 2 line display
#ifdef LCD_I2C
 #include <LiquidCrystal_I2C.h>             // https://bitbucket.org/fmalpartida/new-liquidcrystal/overview (old: https://github.com/fdebrabander/Arduino-LiquidCrystal-I2C-library)
 LiquidCrystal_I2C lcd(LCD_ADDR, LCD_LED, POSITIVE); //, LCD_CHARS, LCD_LINES);
#else
 #include <LiquidCrystal.h>
 LiquidCrystal lcd(LCD_RS, LCD_EN, LCD_D4, LCD_D5, LCD_D6, LCD_D7);
#endif

#include "Debug.h"
#include "Tools.h"

// esp-link connected
#ifdef HAVE_ESPLINK
 #include <ELClient.h>
 #include <ELClientRest.h>
 // Initialize a connection to esp-link using the normal hardware serial port both for
 // SLIP and for debug messages.
#ifdef DEBUG
 ELClient esp(&Serial, &Serial);
#else
 // ELClient esp(&Serial); // suspected to crash el-client?
 ELClient esp(&Serial, &Serial);
#endif
 // Initialize a REST client on the connection to esp-link
 ELClientRest rest(&esp);
#endif


// ä \341
// ü \365
// ö \357
// ° \337

#ifdef DHTPIN_I
 DHT dht_i(DHTPIN_I, DHTTYPE_I);
#endif
#ifdef DHTPIN_O
 DHT dht_o(DHTPIN_O, DHTTYPE_O);
#endif
#ifdef BMEI2C1
 BME280_I2C sens_i(BMEI2C1); 
#endif
#ifdef BMEI2C2
 BME280_I2C sens_o(BMEI2C2); 
#endif
#ifdef SHTI2C1
 cactus_io_SHT31 sens_i(SHTI2C1); 
#endif
#ifdef SHTI2C2
 cactus_io_SHT31 sens_o(SHTI2C2); 
#endif


// ----------------------------------------------


void timerIsr()
{
  Encoder.service();
}

// function prototypes
double DewPoint(double akt_temp, double humidity);
void trigger_backlight(void);
void update_screen(uint8_t screen);
void do_measure(void);
void show_activity(void);
bool check_switch_rules(uint8_t dev, uint8_t dewp_i, uint8_t dewp_o);
void dev_stop(uint8_t is_stop, uint8_t mydev);
void sprint_report(void);
// end function prototypes

#ifdef HAVE_ESPLINK
 #include "Esplink.h"
#endif

void setup() {
  pinMode(ActLED, OUTPUT);
  pinMode(Relais_L, OUTPUT);
  pinMode(Relais_E, OUTPUT);
#ifdef BUZZER  
 pinMode(BUZZER, OUTPUT);
#endif

  // Alles aus
//  set_relay(0, false);              // Lüfter ausschalten
//  set_relay(1, false);              // Entf. ausschalten

  Timer1.initialize(4000);  // 1000000 = 1s
  Timer1.attachInterrupt(timerIsr);

  OUT_SERIAL(SERIAL_BAUD); // initialize only for if DEBUG or HAVE_ESPLINK

  // LCD
#ifdef LCD_I2C
  lcd.begin(LCD_CHARS, LCD_LINES);
#else
  pinMode(LCD_LED, OUTPUT);
  lcd.begin(LCD_CHARS, LCD_LINES);
#endif
  lcd.createChar(IconHeart, heart);
  lcd.createChar(IconLeft,  left);
  lcd.createChar(IconRight, right);
  lcd.createChar(IconBack,  back);
  lcd.createChar(IconBlock, block);

  lcd.clear();
  trigger_backlight();
  
  //         0123456789012345
  FPL(HEADER1);
  lcd.print(VERSION);
  lcd.setCursor(0, 1);
  FPL(HEADER2);
  delay(1500);
  lcd.setCursor(0, 1);
  FPL(HEADER3);
  delay(1500);
  lcd.setCursor(0, 1);
  FPL(HEADER4);
  buzzer(150);
  delay(2000);

  // read params from eeprom
  // if no valid settings found in EEPROM, or button is pressed => set to default values
  ClickEncoder::Button b = Encoder.getButton();          // pressed during Startup?
  lcd.setCursor(0, 1);
  lcd.write(IconRight);
  int16_t val = word(EEPROM.read(EEPROM_ADDR), EEPROM.read(EEPROM_ADDR+1));
  //if (word(EEPROM.read(EEPROM_ADDR), EEPROM.read(EEPROM_ADDR+1)) < 10 || word(EEPROM.read(EEPROM_ADDR), EEPROM.read(EEPROM_ADDR+1)) > 100 || (b != ClickEncoder::Open)) 
  if (val < 10 || val>100 || (b != ClickEncoder::Open))
  {
    write_to_eeprom();
    FPL(OutDefaults);
  } else {
    // load settings from EEPROM
    read_from_eeprom();
    FPL(OutLoaded);
#ifndef HAVE_ESPLINK
    cust_params[HAVE_WIFI] = 0;  // override eeprom in case of changed ESP-link config
#endif

#ifdef FAKE
    cust_params[HAVE_DEHYD] = 0;
    cust_params[MAX_LRUN] = 6;
    cust_params[L_PAUSE] = 5;
#endif
  }
  delay(2000);

  OUT_SERLN("");
  OUT_SER(F("Prima Kellerklima "));
  OUT_SERLN(VERSION);

  sprint_report();
 
  engine = new Menu::Engine(&Menu::NullItem);
  //menuExit(Menu::actionNone); // reset to initial state

  // LCD
  //lcd.home();
  lcd.clear();
  FPL(OutTrigger);
  lcd.print(cust_params[HUM_MAX]);
  lcd.print("%");
  lcd.setCursor(0, 1);
  //         0123456789012345
  FPL(dTau);
  lcd.print(cust_params[HYSTERESIS_HUM]);
  lcd.print("\337C / ");
  lcd.print(cust_params[TAUPUNKTDIFF_ON]);
  lcd.print("\337C ");
  delay(2000);

  // initialize Sensors
#ifdef DHTPIN_I
  dht_i.begin();
#endif
#ifdef DHTPIN_O
  dht_o.begin();
#endif
#ifdef I2C_SENSOR1
 if (!sens_i.begin()) {
      DEBUG_PRINTLN(F("Failed to read from indoor sensor (S1)!"));
      FPL(OutErrSensor);
      lcd.print("S1!");
      buzzer(0);
 }
#endif
#ifdef I2C_SENSOR2
 if (!sens_o.begin()) {
      DEBUG_PRINTLN(F("Failed to read from outdoor sensor (S2)!"));
      FPL(OutErrSensor);
      lcd.print("S2!");
      buzzer(0);
 }
 // calibration
 //sens_i.setTempCal(-1);// Temp was reading high so subtract 1 degree
 //sens_o.setTempCal(-1);// Temp was reading high so subtract 1 degree
#endif

#ifdef HAVE_ESPLINK
 setup_wifi();
#endif

  OUT_SERLN(F("---------- END OF SETUP PHASE ----------"));
  delay(2000);
}

void loop() { 
int16_t *iValue;
//uint32_t last_days;

#ifdef HAVE_ESPLINK
// process ESP-link events
  if(cust_params[HAVE_WIFI]) {   
    esp.Process();
  }
#endif
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

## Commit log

2018-02-10 support passive buzzer
    needed 4mm footprint buzzer = passive only
    (pwm version)
    [Config.h, Tools.h]
2018-02-17 added PCB version
    schematics and gerbers added
    [Kellerklima-B.Cu.gbr, Kellerklima-B.Mask.gbr, Kellerklima-B.Paste.gbr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]
2019-02-28 version 1.2
    update for V1.2 stable
    [Kellerklima-B.Cu.gbr, Kellerklima-B.Mask.gbr, Kellerklima-B.Paste.gbr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]
2019-03-01 added serial error reporting (failing sensors)
    [Config.h, Kellerklima.ino]
2019-09-15 hardware and software fixes
    fixed sensor PCB
    fixed software (hysteresis, operation of dehumidifier)
    [Kellerklima.drl]
2019-09-15 added KiCAD project files
    project files for sensor and main PCB added
    [Kellerklima.kicad_pcb, Kellerklima.sch, SensorPCB_V1.2.kicad_pcb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]
2019-10-29 new hysteresis and dewpoint handling
    using hysteresis for humidity comparison
    using upper and lower dew point diffs for switching
    better runtime control
    bug fixes
    [Config.h, Kellerklima.ino, Tools.h]
2019-11-02 more fixes
    fixed some visuals
    some cleanup
    more bugs fixed
    [Kellerklima.ino]
2019-11-02 code cleanup
    more code cleanup
    integer bug fixed
    [Config.h, Kellerklima.ino, Tools.h]
2019-11-13 some more cleanup
    * removed some obsolete stuff
    * added some more debug msgs for remote sessions
    * fixed wrong dev_stop type
    [Config.h, Kellerklima.ino, Tools.h]
2019-11-25 bug fixes, temp. calibration
    fixed some lazy type defs
    added new parameters for temperature compensation offsets (LCD and remote)
    [Config.h, Kellerklima.ino, Tools.h]
